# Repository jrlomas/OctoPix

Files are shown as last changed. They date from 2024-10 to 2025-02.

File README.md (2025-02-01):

# OctoPix Expansion PCB for BTT Octopus Board

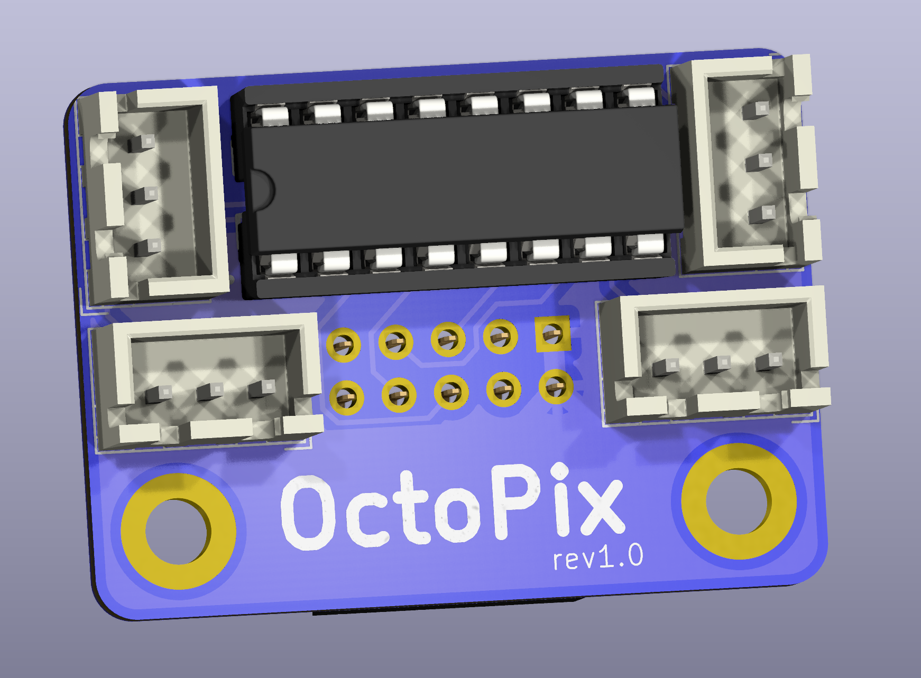
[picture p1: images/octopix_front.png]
OctoPix Front View

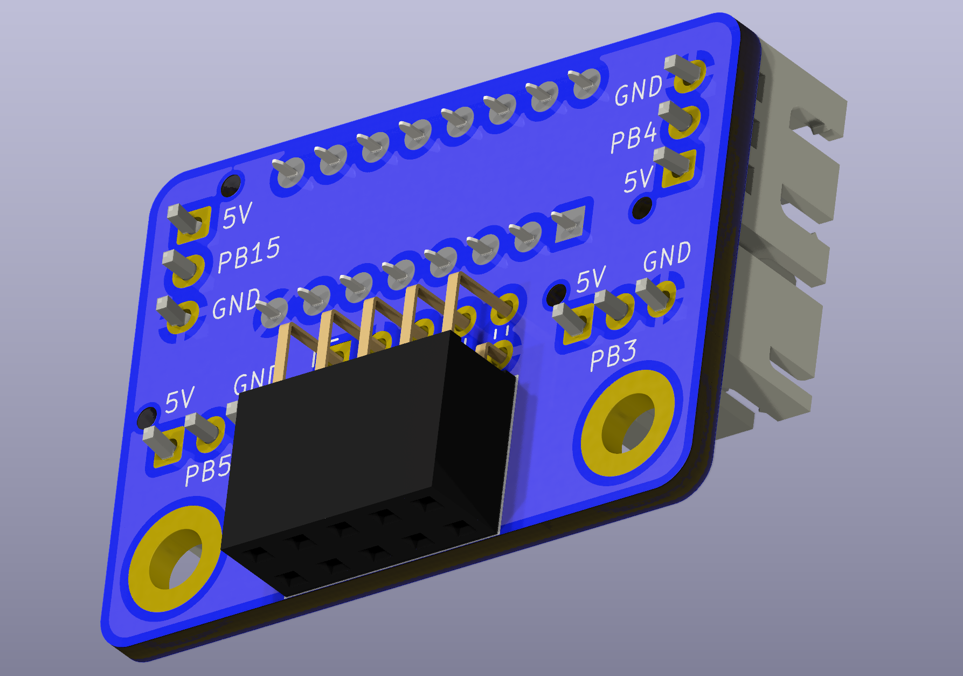
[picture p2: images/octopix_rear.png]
OctoPix Rear View


This PCB expansion board adds additional Neopixel outputs to your BTT Octopus board, allowing for custom RGB lighting configurations. It plugs into the Octopus's SPI3 header (J47) and provides four JST-XH 3-pin connectors to support up to four separate Neopixel connections.

## Features

- **4x JST-XH 3-pin connectors** for Neopixel data connections
- Compatible with the **BTT Octopus** control board for 3D printers
- Designed to plug directly into the **SPI3 (J47)** header on the Octopus
- Compact design fits neatly without obstructing other ports or components on the Octopus board
- **Buffered data signals** using a **CD4050B** (DIP 16 package) for reliable Neopixel communication

## Bill of Materials (BOM)

| Quantity | Part Description | Example Sourcing Links |
|---|---|---|
| 4 | JST-XH 3-pin connectors | [DigiKey](https://www.digikey.com/en/products/detail/jst-sales-america-inc/B3B-XH-A/1651046) |
| 1 | 2x5 header, 2.54mm pitch (Sullins SFH11-PBPC-D05-RA-BK) | [DigiKey SFH11-PBPC-D05-RA-BK](https://www.digikey.com/en/products/detail/sullins-connector-solutions/SFH11-PBPC-D05-RA-BK/1990095) |
| 1 | CD4050B (DIP 16 package) | [DigiKey](https://www.digikey.com/en/products/detail/texas-instruments/CD4050BE/67303) |

## Installation

1. Align the OctoPix PCB with the **J47 SPI3 header** on the Octopus board.
2. Gently press the OctoPix PCB into the J47 header until fully seated.
3. Connect your Neopixel strips to the 3-pin JST-XH connectors on the OctoPix PCB.
4. Power on your Octopus board and configure your Neopixel effects using your preferred firmware (e.g., Klipper, Marlin).

**OctoPix PCB Installed on BTT Octopus Board** (front and rear views):
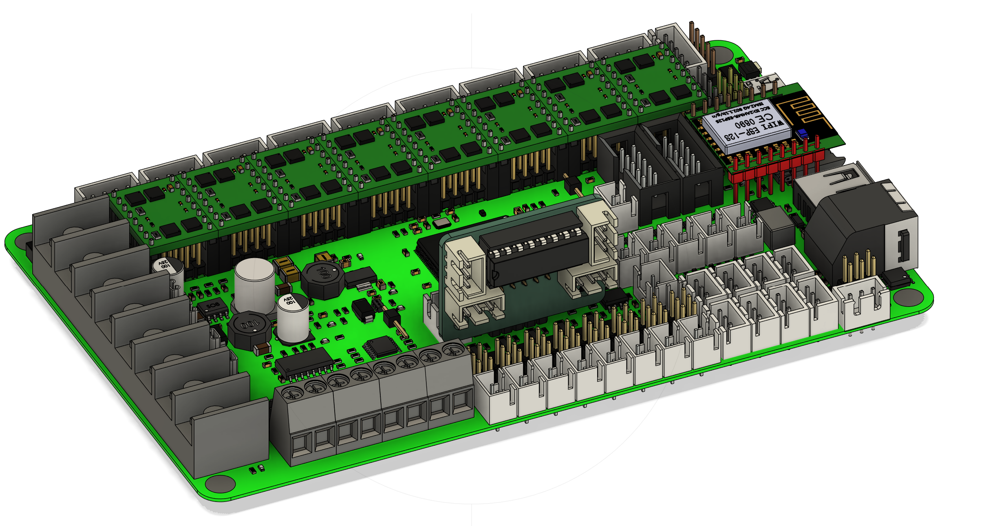
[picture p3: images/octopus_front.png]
Installed Front View

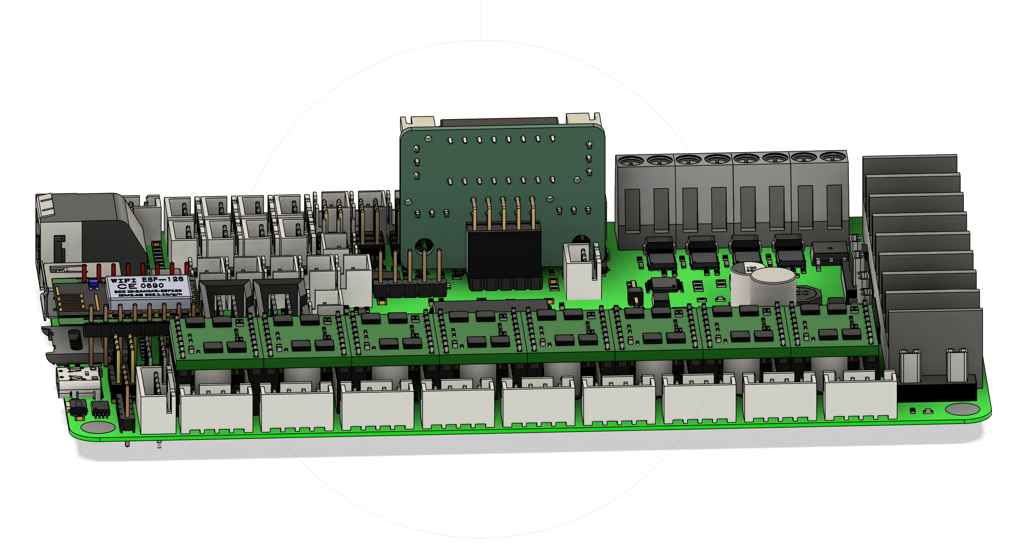
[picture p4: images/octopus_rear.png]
Installed Rear View


## Known Issues & Solutions

Some users have reported the isssue that when assigning PB3, PB4, and PB5 to neopixels, klipper reports the pins as already being assigned to ``spi3`` (specially in STM32F446 MCUs).
If you get this problem when restarting klipper, the solution is to recompile klipper firmware commenting out the lines below, found in the source code under ``~/klipper/src/stm32/spi.c``:

```
 DECL_ENUMERATION("spi_bus", "spi3", 4);
 DECL_CONSTANT_STR("BUS_PINS_spi3", "PB4,PB5,PB3");
```

The lines should instead read:

```
//DECL_ENUMERATION("spi_bus", "spi3", 4);
//DECL_CONSTANT_STR("BUS_PINS_spi3", "PB4,PB5,PB3");
```

After re-compiling and flashing the Octopus, PB3, PB4, and PB5 should be free to be used as GPIO pins instead of being bound to ``spi3``

## Credits

This project was created by **knight_rad.iant** on Discord. Join the discussion and follow updates on the design.

---

Contributions, suggestions, and improvements are welcome. Please open an issue or submit a pull request if you have ideas to enhance this project.

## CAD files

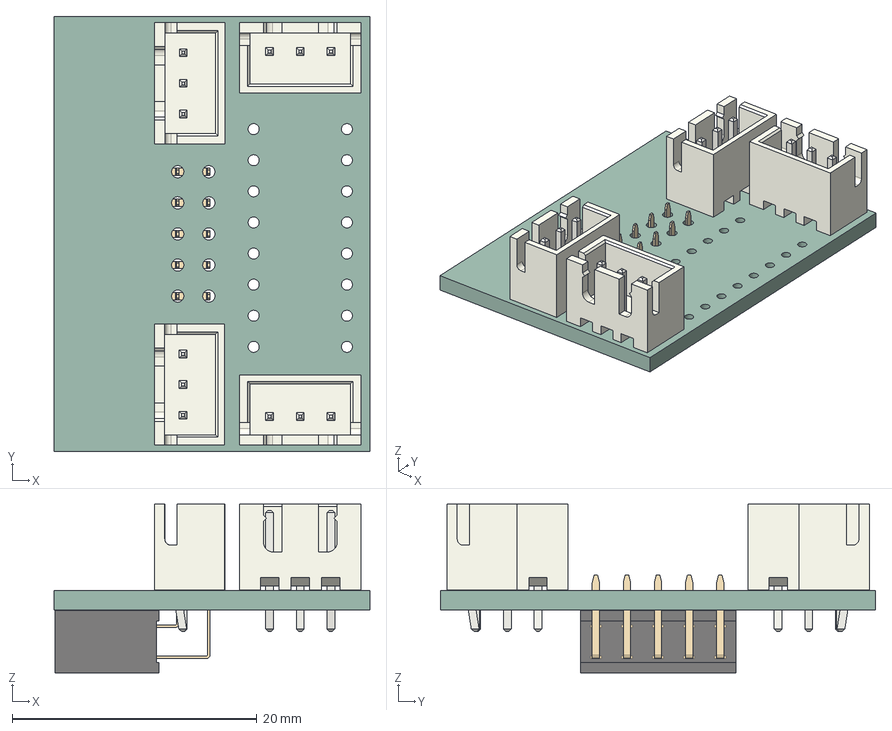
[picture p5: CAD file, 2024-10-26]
octopixel.step
25.8 x 35.5 x 13.8 mm
JST_B3B_XH_A x 4
PinSocket_2x05_P254mm_Horizontal
octopixel_PCB

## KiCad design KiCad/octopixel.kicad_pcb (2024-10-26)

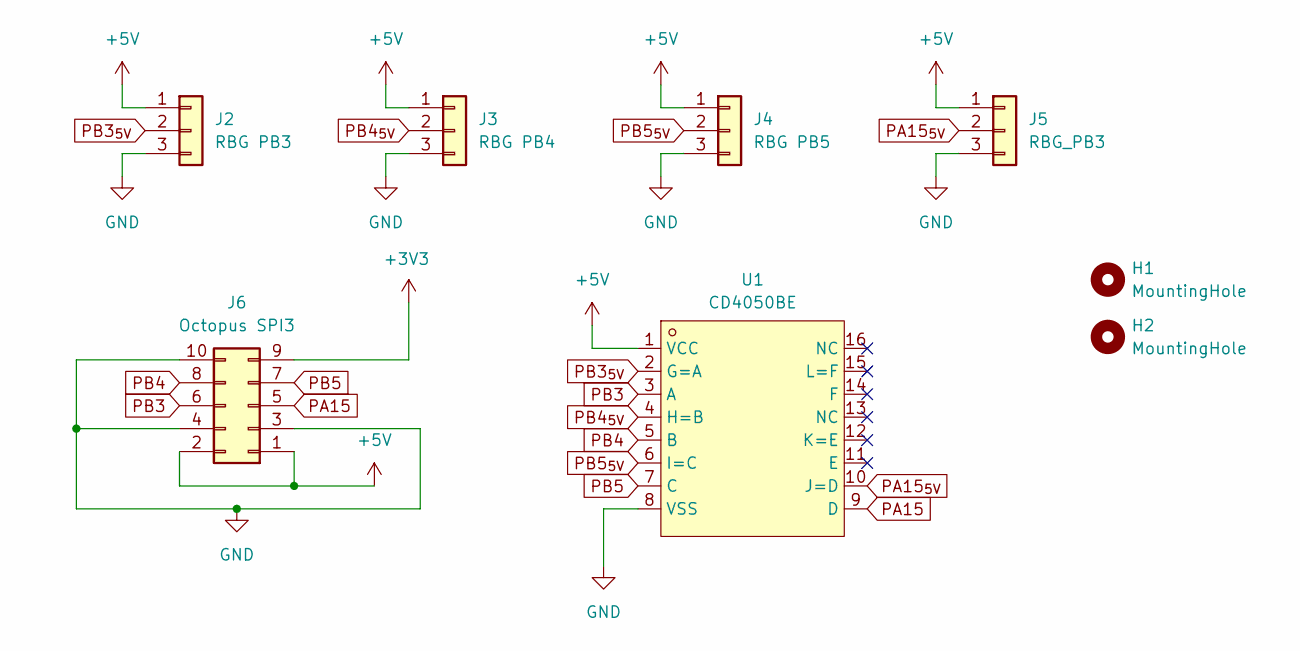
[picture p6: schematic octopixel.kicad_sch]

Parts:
H1, H2: MountingHole; MountingHole_3.2mm_M3_DIN965_Pad
J2: RBG PB3; JST_XH_B3B-XH-AM_1x03_P2.50mm_Vertical
J3: RBG PB4; JST_XH_B3B-XH-AM_1x03_P2.50mm_Vertical
J4: RBG PB5; JST_XH_B3B-XH-AM_1x03_P2.50mm_Vertical
J5: RBG_PB3; JST_XH_B3B-XH-AM_1x03_P2.50mm_Vertical
J6: Octopus SPI3; PinSocket_2x05_P2.54mm_Horizontal
U1: CD4050BE; DIP-16_L20.3-W10.2-P2.54-LS10.2-BL; LCSC Part C5223

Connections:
+3V3: J6.9
+5V: J2.1, J3.1, J4.1, J5.1, J6.1, J6.2, U1.1 (VCC)
GND: J2.3, J3.3, J4.3, J5.3, J6.3, J6.4, J6.10, U1.8 (VSS)
PA15: J6.5, U1.9 (D)
PA15_{5V}: J5.2, U1.10 (J=D)
PB3: J6.6, U1.3 (A)
PB3_{5V}: J2.2, U1.2 (G=A)
PB4: J6.8, U1.5 (B)
PB4_{5V}: J3.2, U1.4 (H=B)
PB5: J6.7, U1.7 (C)
PB5_{5V}: J4.2, U1.6 (I=C)

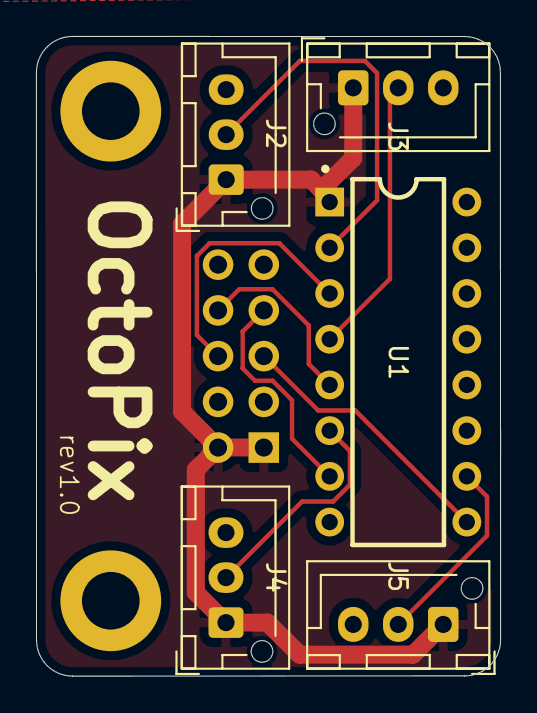
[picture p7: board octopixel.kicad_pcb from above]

Board: 2 copper layers, 25.8 x 35.5 mm, 8 parts (1 on the bottom side), 10 nets.

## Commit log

2024-10-26 OctoPix initial commit
    [octopixel.kicad_pcb, octopixel.kicad_sch, octopixel.step]
2024-10-26 Updated step file
    [octopixel.kicad_pcb]
2024-10-26 Reorganization of project
    [octopixel.kicad_pcb, octopixel.kicad_sch]
